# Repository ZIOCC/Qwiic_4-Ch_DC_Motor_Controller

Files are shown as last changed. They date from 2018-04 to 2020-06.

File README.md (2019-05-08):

# Zio Qwiic 4 DC Motor Controller

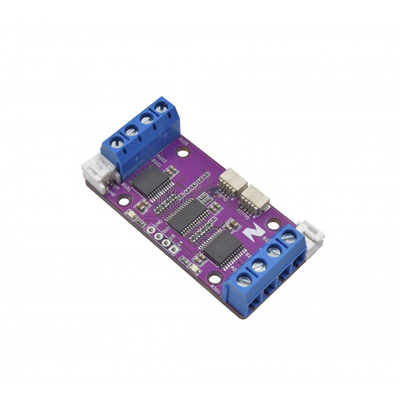
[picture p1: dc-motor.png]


> This product can be available for purchase [here](https://www.smart-prototyping.com/Zio-4-DC-Motor-Controller.html).

#### Description

Drive two motors at up to 1.2A of constant current with the Zio Bidirectional 4-Channel DC Motor Controller. Dual H-bridges will allow you to also brake and stop in addition to controlling the direction and speed of the motors. Two input signals (IN1 and IN2) can be used to control the motors with the following functions: CW, CCW, short-brake, and stop. 

You can independently control the two bidirectional DC motors at once. The PWM input allows you to spin the wheels in either direction and at whatever speed you like.

This board also comes equipped with Qwiic connectors so you can quickly and easily daisy-chain to other modules in the Qwiic ecosystem.

> Note: As with all of the Version 1.0 Zio Qwiic boards, this board has been produced with the I2C pull-ups disconnected by default. If there's a significant length of wire between this board and your MCU, you'll need to solder closed the solder jumpers (labeled SDA, 3v3 and SCL) to connect the pull-up resistors to VCC.

#### Specification

* Recommended motor voltage is 2.7 - 5.5V with a max of 15V (For full-current operation at higher voltages, add an appropriate heatsink to prevent triggering the thermal shutdown circuit and to keep the magic smoke inside those precious H-bridges)
* Output current continuous: 1A per channel
* Max. PWM Frequency: 100kHz
* Built-in Power Saving System
* Built-in Thermal Shutdown Circuit and Low Voltage Detecting Circuit
* IC: PCA9685
* I2C address: 0x40-0x7F (default: 0x40)
* Weight: 12.9g (0.45oz)
* Dimension: 54.2x27mm

#### Links

* [PCA9685PW datasheet](https://www.smart-prototyping.com/image/data/NOA-RnD/101897%204%20DC%20Motor%20Driver/PCA9685PW_datasheet.pdf)
* [TB6612FNG datasheet](https://www.smart-prototyping.com/image/data/NOA-RnD/101897%204%20DC%20Motor%20Driver/TB6612FNG_datasheet.pdf)
* [Adafruit PWM Servo Driver Library](https://github.com/adafruit/Adafruit-PWM-Servo-Driver-Library)
* [Demo Code (Solder the pull-up jumpers)](https://www.smart-prototyping.com/image/data/NOA-RnD/101897%204%20DC%20Motor%20Driver/Zio_4_DC_Motor_Controller.ino)
* [Eagle files](https://github.com/ZIOCC/Qwiic_4-Ch_DC_Motor_Controller)

##### Connections for demo


> ###### About Zio
> Zio is a new line of open sourced, compact, and grid layout boards, fully integrated for Arduino and Qwiic ecosystem. Designed ideally for wearables, robotics, small-space limitations or other on the go projects. Check out other awesome Zio products [here](https://www.smart-prototyping.com/Zio).

> All Zio products are released under the [Creative Commons Attribution, Share-Alike License](https://creativecommons.org/licenses/by-sa/4.0/), and in accordance with the principles of the [Open Source Hardware Association's OSHW Statement of Principles 1.0 and OSHW Definition 1.0](https://www.oshwa.org/definition/).

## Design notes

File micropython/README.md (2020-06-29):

#### Usage
This library can control up to 4 DC motors by I2C interface. The I2C usually can't support big current for motors, so please use extenal power for the driver board. 

#### Demo code: 
The following demo code will slowly speed up the motor, everytime the motor will go forward first, then go back.
```  
from machine import Pin,I2C
import qwiic_motor

i2c = I2C(sda=Pin("Y10"), scl=Pin("Y9"))
print(i2c.scan())

mt = qwiic_motor.DCMOTOR(i2c=i2c, addr=0x40, freq=1000)
pyb.delay(1000)

while True:

    for i in range(0,100):
        mt.go_ahead(0)
        mt.speed(0,i)
        print("cw speed:" + str(i))
        pyb.delay(1000)
        mt.go_back(0)
        mt.speed(0,i)
        print("ccw speed:" + str(i))
        pyb.delay(1000)
    mt.stop(0)
    pyb.delay(1000)

```  

#### Note: 
1. go_ahead() will not make the motor move, it just sets a direction, you need to use speed() method to add speed. 
2. When the speed is close to 0, ususally the motor will not move. 
3. Motor name on the board and relavent number.
Motor Name | Motor NO. |
 ---- | ----- 
A101  | 0 
B101  | 1 
A201|2
b201|3

#### Product link: 
[Qwiic DC motor driver board](https://www.smart-prototyping.com/Zio-4-DC-Motor-Controller.html)

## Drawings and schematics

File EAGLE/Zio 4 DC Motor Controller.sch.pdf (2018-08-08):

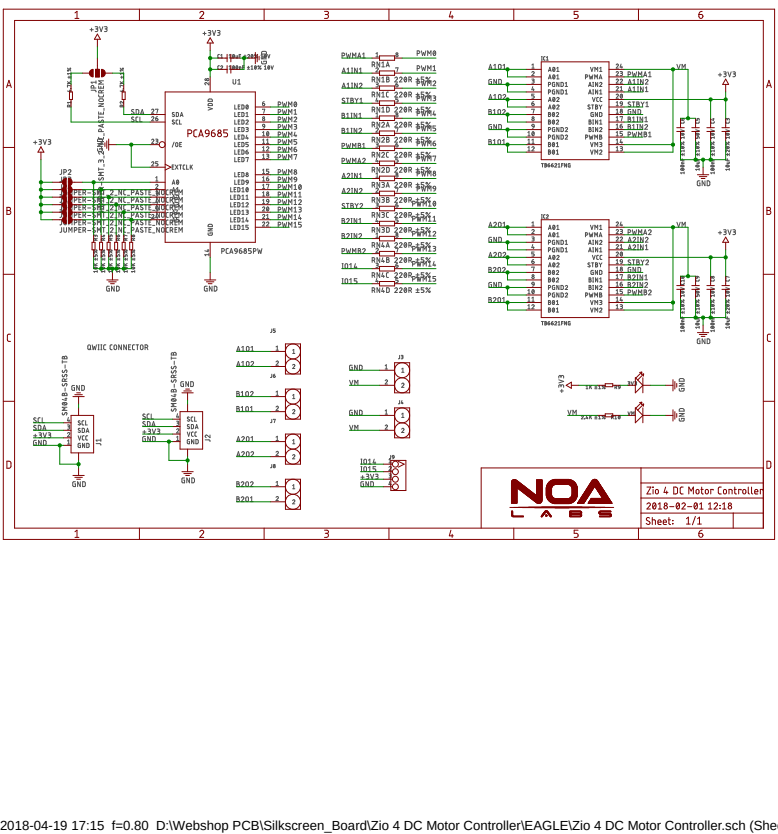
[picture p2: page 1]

2018-04-19 17:15 f=0.80 D:\Webshop PCB\Silkscreen_Board\Zio 4 DC Motor Controller\EAGLE\Zio 4 DC Motor Controller.sch (Sheet: 1/1)

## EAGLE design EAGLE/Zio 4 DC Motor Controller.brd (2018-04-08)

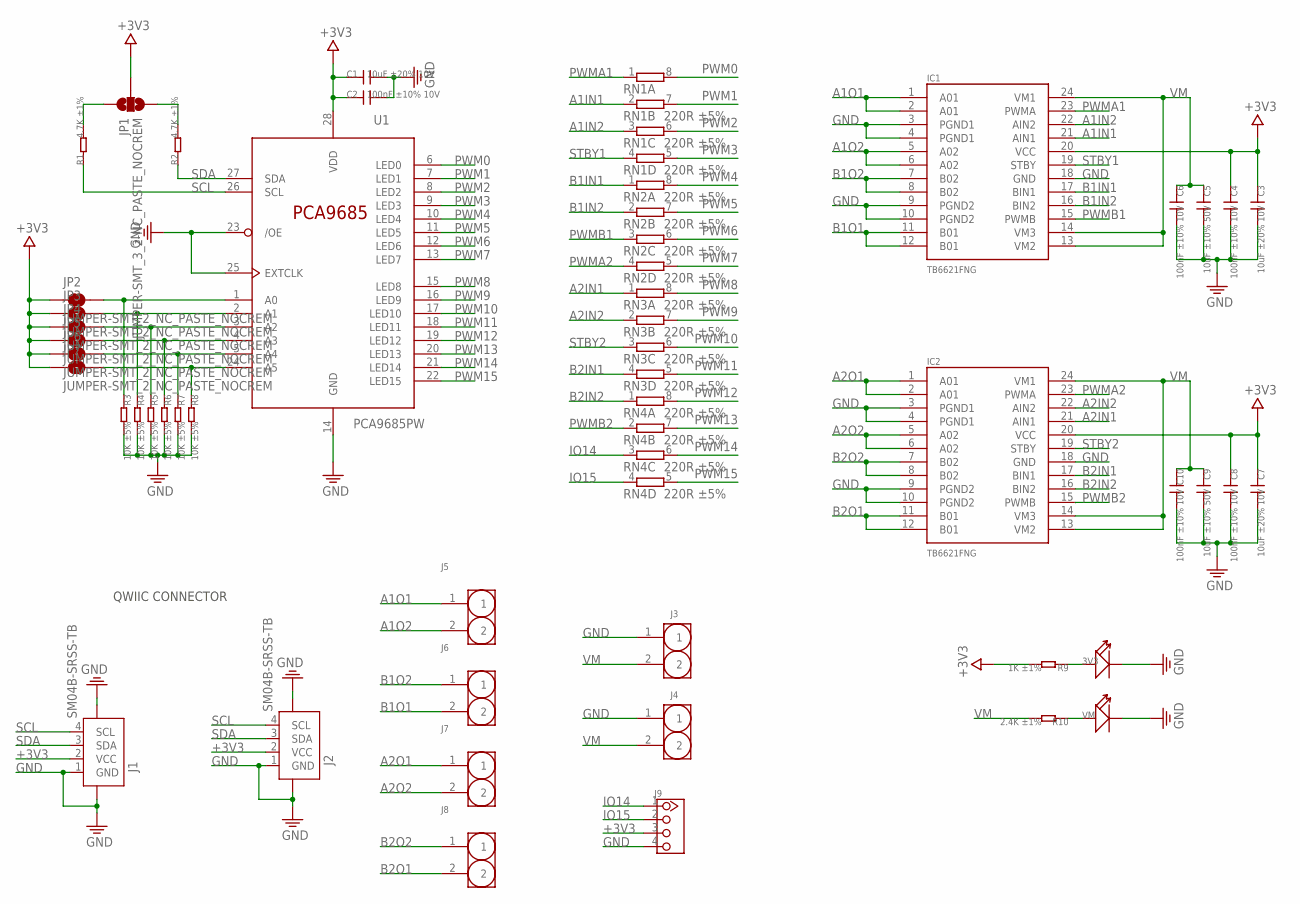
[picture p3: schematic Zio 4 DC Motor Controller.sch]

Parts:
3V3: LED'0805'; LED-0805
C1, C3, C7: 10uF ±20% 10V; 0603
C2, C4, C6, C8, C10: 100nF ±10% 10V; 0603
C5, C9: 10uF ±10% 50V; 0805
IC1, IC2: TB6621FNG; SSOP24
J1, J2: SM04B-SRSS-TB; JST-SH-4P
J3, J4: HEADER-2P-2.0-90; PH2.0-2P-90
J5, J6, J7, J8: HEADER-2P-SCREW5.0; 2P-SCREW-5.0
J9: HEADER-4P-80/40MIL; 4P-2.54-80/40MIL
JP1: JUMPER-SMT_3_2-NC_PASTE_NOCREM; SMT-JUMPER_3_2-NC_PASTE_SILK_NOCREM
JP2, JP3, JP4, JP5, JP6, JP7: JUMPER-SMT_2_NC_PASTE_NOCREM; SMT-JUMPER_2_NC_PASTE_SILK_NOCREM
R1, R2: 4.7K ±1%; 0603
R3, R4, R5, R6, R7, R8: 10K ±5%; 0402
R9: 1K ±1%; 0603
R10: 2.4K ±1%; 0603
RN1, RN2, RN3, RN4: 220R ±5%; RESISTOR-DIL_0603-ARV
U1: PCA9685PW; TSSOP28
VM: LED'0805'; LED-0805

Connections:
+3V3: C1.1, C2.1, C3.1, C4.1, C7.1, C8.1, IC1.20 (VCC), IC2.20 (VCC), J1.2 (VCC), J2.2 (VCC), J9.3, JP1.2, JP2.1, JP3.1, JP4.1, JP5.1, JP6.1, JP7.1, R9.2, U1.28 (VDD)
A1IN1: IC1.21 (AIN1), RN1.2 (1)
A1IN2: IC1.22 (AIN2), RN1.3 (1)
A1O1: IC1.1 (A01), IC1.2 (A01), J5.1
A1O2: IC1.5 (A02), IC1.6 (A02), J5.2
A2IN1: IC2.21 (AIN1), RN3.1
A2IN2: IC2.22 (AIN2), RN3.2 (1)
A2O1: IC2.1 (A01), IC2.2 (A01), J7.1
A2O2: IC2.5 (A02), IC2.6 (A02), J7.2
B1IN1: IC1.17 (BIN1), RN2.1
B1IN2: IC1.16 (BIN2), RN2.2 (1)
B1O1: IC1.11 (B01), IC1.12 (B01), J6.2
B1O2: IC1.7 (B02), IC1.8 (B02), J6.1
B2IN1: IC2.17 (BIN1), RN3.4 (1)
B2IN2: IC2.16 (BIN2), RN4.1
B2O1: IC2.11 (B01), IC2.12 (B01), J8.2
B2O2: IC2.7 (B02), IC2.8 (B02), J8.1
GND: 3V3.-, C1.2, C2.2, C3.2, C4.2, C5.2, C6.2, C7.2, C8.2, C9.2, C10.2, IC1.3 (PGND1), IC1.4 (PGND1), IC1.9 (PGND2), IC1.10 (PGND2), IC1.18 (GND), IC2.3 (PGND1), IC2.4 (PGND1), IC2.9 (PGND2), IC2.10 (PGND2), IC2.18 (GND), J1.1 (GND), J1.NC1 (5), J1.NC2 (6), J2.1 (GND), J2.NC1 (5), J2.NC2 (6), J3.1, J4.1, J9.4, R3.2, R4.2, R5.2, R6.2, R7.2, R8.2, U1.14 (GND), U1.23 (/OE), U1.25 (EXTCLK), VM.-
IO14: J9.1, RN4.3 (1)
IO15: J9.2, RN4.4 (1)
unnamed: JP2.2, R3.1, U1.1 (A0)
unnamed: JP3.2, R4.1, U1.2 (A1)
unnamed: JP4.2, R5.1, U1.3 (A2)
unnamed: JP5.2, R6.1, U1.4 (A3)
unnamed: JP6.2, R7.1, U1.5 (A4)
unnamed: JP7.2, R8.1, U1.24 (A5)
unnamed: 3V3.+, R9.1
unnamed: R10.1, VM.+
unnamed: JP1.1, R1.2
unnamed: JP1.3, R2.2
PWM0: RN1.8 (2), U1.6 (LED0)
PWM1: RN1.7 (2), U1.7 (LED1)
PWM2: RN1.6 (2), U1.8 (LED2)
PWM3: RN1.5 (2), U1.9 (LED3)
PWM4: RN2.8 (2), U1.10 (LED4)
PWM5: RN2.7 (2), U1.11 (LED5)
PWM6: RN2.6 (2), U1.12 (LED6)
PWM7: RN2.5 (2), U1.13 (LED7)
PWM8: RN3.8 (2), U1.15 (LED8)
PWM9: RN3.7 (2), U1.16 (LED9)
PWM10: RN3.6 (2), U1.17 (LED10)
PWM11: RN3.5 (2), U1.18 (LED11)
PWM12: RN4.8 (2), U1.19 (LED12)
PWM13: RN4.7 (2), U1.20 (LED13)
PWM14: RN4.6 (2), U1.21 (LED14)
PWM15: RN4.5 (2), U1.22 (LED15)
PWMA1: IC1.23 (PWMA), RN1.1
PWMA2: IC2.23 (PWMA), RN2.4 (1)
PWMB1: IC1.15 (PWMB), RN2.3 (1)
PWMB2: IC2.15 (PWMB), RN4.2 (1)
SCL: J1.4 (SCL), J2.4 (SCL), R1.1, U1.26 (SCL)
SDA: J1.3 (SDA), J2.3 (SDA), R2.1, U1.27 (SDA)
STBY1: IC1.19 (STBY), RN1.4 (1)
STBY2: IC2.19 (STBY), RN3.3 (1)
VM: C5.1, C6.1, C9.1, C10.1, IC1.13 (VM2), IC1.14 (VM3), IC1.24 (VM1), IC2.13 (VM2), IC2.14 (VM3), IC2.24 (VM1), J3.2, J4.2, R10.2

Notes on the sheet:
QWIIC CONNECTOR

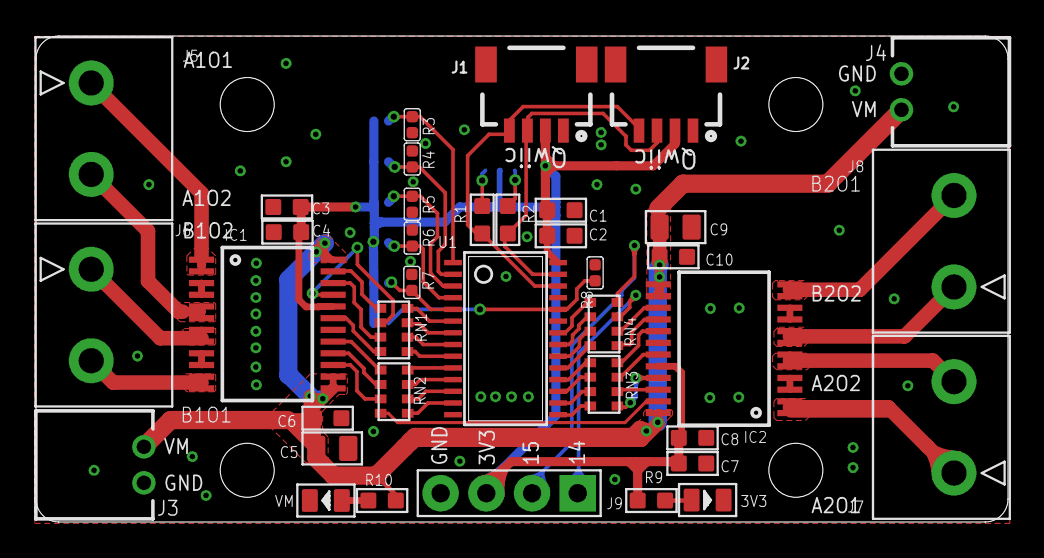
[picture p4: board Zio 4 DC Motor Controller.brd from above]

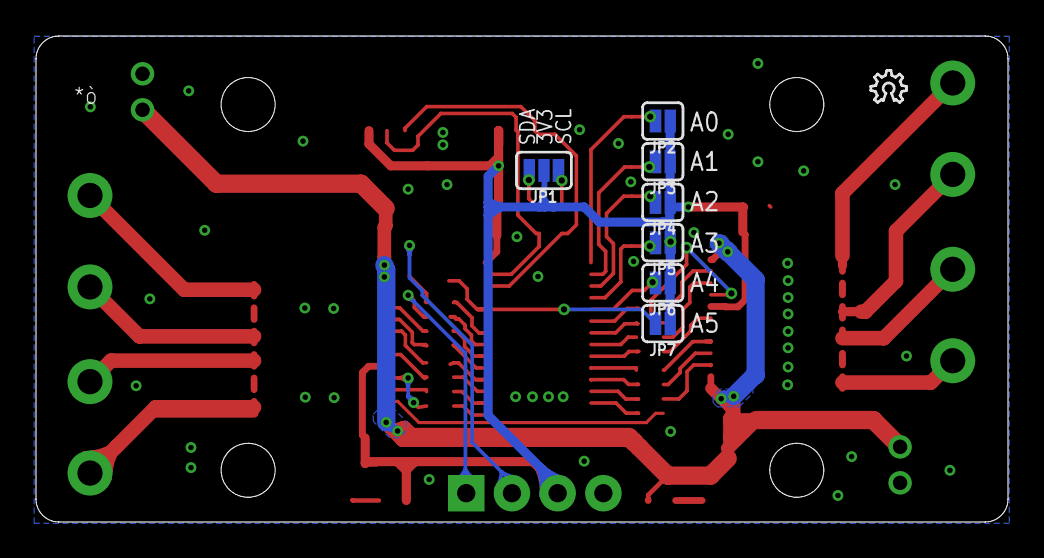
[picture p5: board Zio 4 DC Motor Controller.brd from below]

Board: 2 copper layers, 54.0 x 27.0 mm, 48 parts (9 on the bottom side), 55 nets.

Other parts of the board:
E$11: 10MM
LOGO1: LOGO-OSHW-6MILX0070-NT; OSHW_6X70_NOTEXT
U$5: 6MM

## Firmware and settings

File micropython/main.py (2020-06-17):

from machine import Pin,I2C
import motor


i2c = I2C(sda=Pin("Y10"), scl=Pin("Y9"))
print(i2c.scan())

mt = motor.DCMOTOR(i2c=i2c, addr=0x40, freq=1000)
pyb.delay(1000)

while True:

    for i in range(10,50):
        mt.motor_go_ahead(0)
        mt.motor_speed(0,i)
        print("cw speed:" + str(i))
        pyb.delay(1000)
        mt.motor_go_back(0)
        mt.motor_speed(0,i)
        print("ccw speed:" + str(i))
        pyb.delay(1000)
    mt.motor_stop(0)
    pyb.delay(1000)
